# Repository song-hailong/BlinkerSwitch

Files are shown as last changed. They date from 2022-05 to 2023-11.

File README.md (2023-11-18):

# Blinker-Switch

通过改造墙壁开关，实现语音控制灯的效果。接入的平台为点灯科技，语音助手为小爱同学，可改造成天猫精灵和百度小度。

视频链接为： [【blinker】1：ESP8266点灯科技开发环境搭建](https://www.bilibili.com/video/BV1sk4y127Ab/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)  [【blinker】2：语音开关灯，墙壁开关改造篇！](https://www.bilibili.com/video/BV1dz4y1f7gt/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)

Blinker开发环境搭建可根据文档 **[点灯科技开发环境搭建](https://www.songhailong.cn/2022/05/%E7%82%B9%E7%81%AF%E7%A7%91%E6%8A%80%E5%BC%80%E5%8F%91%E7%8E%AF%E5%A2%83%E6%90%AD%E5%BB%BA/)** 进行操作。

PlatformIO IDE开发环境搭建可根据 [VSCode 下 PlatformIO 的安装教程](https://songhailong.cn/2023/01/VSCode%E4%B8%8BPlatformIO%E7%9A%84%E5%AE%89%E8%A3%85%E6%95%99%E7%A8%8B/) 进行安装。

---

# 常见问题：

1. 米家同步后无设备：需设备在线时点同步。
2. 米家APP设备页不显示该设备：点灯科技只能接入小爱同学，不能显示在米家主页，只会在其他平台设备页显示。如需设置与米家设备联动，可选择 **小爱音响 -> 自定义指令 -> 输入对应指令（如：”打开客厅的灯泡“） -> 选择静默执行**。

# 更新说明：

更新 3.0.2 版本代码，加入自动配网程序 [WiFiManager](https://github.com/song-hailong/WiFiManager) ，可以上传 key，不需修改代码，直接烧入后配网即可。

设置上电后连上WiFi `AutoConnectAP` ，在弹出的界面进行配网。

new ducument-300

## 一：项目文件介绍

#### 1. **Hardware**

Hardware文件夹为Blinker-Switch电路的原理图和PCB文件，提供Altium Designer格式的源文件。

#### 2. **Software**

Software文件夹为Blinker-Switch的程序源码。

2.1 **Arduino IDE**文件夹为初代程序代码，编译器为Arduino IDE，程序版本号为v2.0，推荐使用，对应的APP界面配置文件为：[界面配置_v2.0.txt](3.%20AppInterface/界面配置_v2.0.txt)。

2.2 **PlatformIO**为后续修改的代码，编译器使用的PlatformIO，程序版本号为v3.0，连续测试一个月后出现卡死，此版本上传数据太多，对于ESP8266来说容易卡死，目前不推荐使用，后续有时间进行优化。对应的APP界面配置文件为：[界面配置_v3.0.txt](3.%20AppInterface/界面配置_v3.0.txt)。

#### 3. AppInterface

AppInterface文件夹中提供了APP界面配置文件，版本号对应程序代码版本号。

#### 4. Docs

相关的参考文件，包括环境搭建和芯片的Datasheet等。

## 二：硬件说明

这款板子是零火版取电的，也就是86盒里面必须要有零线，如果没有的话，可以尝试加入单火取电模块，某宝有卖。

接线图如下：



> AC220V，一定一定要注意安全，一定要断电后操作。

## 三：程序说明

> 3.0.2 版本的代码已加入配网界面，可不修改代码，直接烧入。

将如下代码修改为自己的，设备密匙见下文。



**烧入**：选择对应的串口，以及开发板型号，将程序烧入即可。

## 四：APP配置

将界面配置文件导入到app设备中。

1. 在app中添加设备，获取Secret Key

   进入App，点击右上角的“+”号，然后选择添加设备，点击选择Arduino -> WiFi接入-> 选择要接入的服务商 -> 复制申请到的Secret Key

   Snipaste_2023-11-18_14-23-30

2. DIY界面

   在设备列表页，点击刚才新建的设备图标，进入设备控制面板。首次进入设备控制面板，会弹出向导页，在向导页点击载入示例，即可载入示例组件。点击右上角的修改，选择开关的按钮，样式选择中间那种，按键类型选择：开关按键，再点击有上角的保存。之后我们就可以通过这个按键来控制并查看灯。

   Snipaste_2023-11-18_14-31-04

3. 需导入我配置的界面的话，在APP中打开刚才新建的设备，点击右上角的 **... > 界面配置**，粘贴[界面配置_v2.0.txt](3.%20AppInterface/界面配置_v2.0.txt)中的配置代码即可。

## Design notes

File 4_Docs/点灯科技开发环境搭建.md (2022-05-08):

# 点灯科技开发环境配置
打包好的软件包阿里云链接：https://www.aliyundrive.com/s/KLycuo3tpkM （不定时更新，可到下方链接下载最新版本）。

## 一：安装 Arduino IDE

安装Arduino IDE 1.8.19或更新版本

软件安装包链接： https://www.arduino.cn/thread-5838-1-1.html （来自Arduino论坛）https://www.arduino.cc/en/software （来自官网）

由于某些原因，[Arduino官方网站](https://www.arduino.cc/en/Main/Software)经常打不开或下载速度极慢，推荐论坛下载，下载后安装即可。

## 二：安装ESP8266 SDK

Arduino IDE安装esp8266 SDK。在线安装经常出问题，推荐离线安装。下载链接：https://www.arduino.cn/thread-76029-1-1.html（来自Arduino论坛）。

该帖子里还有ESP32的SDK，可一并下载。下载之后需按照帖子里的要求进行操作：

1. 打开Arduino IDE菜单 > 文件 >首选项，在 **附加开发板管理器网址** 输入框中，填入以下网址：

``` 
https://www.arduino.cn/package_esp8266com_index.json,https://www.arduino.cn/package_esp32_index.jsonhttps://www.arduino.cn/package_esp32_index.json
```

> 若只需安装esp8266的SDK，则只需添加前一个网址即可。ESP32安装的论坛帖子链接为：https://www.arduino.cn/thread-81194-1-1.html。



2. 添加好后，再双击下载好的esp8266和esp32安装包，进行安装即可。

3. 安装好之后，重新打开Arduino IDE，打开 Arduino IDE **菜单 >工具>开发板**，就可以看到ESP8266和ESP32了。

   

## 三：下载blinker Arduino库

下载链接：https://github.com/blinker-iot/blinker-library/archive/refs/heads/dev_3.0.zip

将下载好的blinker库解压到：**我的电脑>文档>Arduino>libraries** 文件夹中



或者通过Arduino IDE进行导入：打开 Arduino IDE **菜单>项目>加载库>添加.ZIP库** ，如下图



两种方法选一种安装即可。

## 四：安装blinker APP

下载链接：https://diandeng.tech/dev



选择对应的安装包安装即可。

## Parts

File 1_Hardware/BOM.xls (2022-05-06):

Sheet: BOM Report
Bill of Materials |  |  | Bill of Materials for Project [ESP8266控制器.PrjPcb] (No PCB Document Selected)
Source Data From: |  | ESP8266控制器.PrjPcb
Project: |  | ESP8266控制器.PrjPcb
Variant: |  | None
Creation Date: | 2020/7/1 | 21:37
Print Date: | 2020-07-01 | 21:38:06
Footprint | Comment | LibRef | Designator | Description | Quantity
M3 125X200 | M3 | M3 | 1, 2, 3, 4 | 铜柱孔 | 4
C 0603_M | 100nF | C | C1 | 无极性贴片电容 | 1
C 0603_M | 104 | C | C2 | 无极性贴片电容 | 1
C 0603_M | 22p | C | C3, C4 | 无极性贴片电容 | 2
C 0603_M | 10uF | C | C5, C6 | 无极性贴片电容 | 2
SMA | SS14 | SS14 | D1, D2, D3 | 肖特基二极管 | 3
CD D(7343) | 100uF | C-CD | E1 | 贴片钽电容 | 1
CD D(7343) | 220uF | C-CD | E2 | 贴片钽电容 | 1
HK4100F | HK4100F-DC5V-SHG | HK4100F | JK1 | 一组转换 | 1
KF301-5.0-2P | HDR-1X2 | Header 2 5.0 | JP1, JP2 | 2P接插件 | 2
SOT23-3N | S8050 | 8050-SMD | Q1, Q2, Q3 | 高频放大-NPN型 | 3
R 0603_M | 12K | R | R1, R2, R3, R4, R5, R10, R11 | 贴片电阻 | 7
R 0603_M | 3k | R | R13, R14 | 贴片电阻 | 2
ESP_12_E_L | ESP_12_E | ESP_12_E | U1 | ESP-12 Wi-Fi Module by AI-Thinker | 1
SOP16_L | CH340G | CH340G | U2 | 串口转USB | 1
SOT223_L | AMS1117-3V3 | AMS1117 | U3 | 三端稳压芯片 | 1
HLK-PM01 | HLK-PM01 | Component_1 | U4 | 220V转5V模块 | 1
USB-MICRO_D | USB-5P | USB-5P | USB1 | 微型USB母座 | 1
OSC HC-49S | 12MHz | XTAL-2P | X1 | 2脚无源脚晶振 | 1
 |  |  |  |  | 36
Approved |  | Notes

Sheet: Project Information
Project Full Path | F:\Project\Altium Designer_Project\ESP8266联网控制器_v2\ESP8266控制器.PrjPcb
Project Filename | ESP8266控制器.PrjPcb
Variant Name | None
Data-Source Filename | ESP8266控制器.PrjPcb
Data-Source Full Path | F:\Project\Altium Designer_Project\ESP8266联网控制器_v2\ESP8266控制器.PrjPcb
Title | Bill of Materials for Project [ESP8266控制器.PrjPcb] (No PCB Document Selected)
Total Quantity | 36
Report Time | 21:37
Report Date | 2020/7/1
Report Date & Tine | 2020/7/1 21:37
Output Name | Bill of Materials
Output Type | BOM_PartType
Output Generator Name | BOM
Output Generator Description | Bill of Materials

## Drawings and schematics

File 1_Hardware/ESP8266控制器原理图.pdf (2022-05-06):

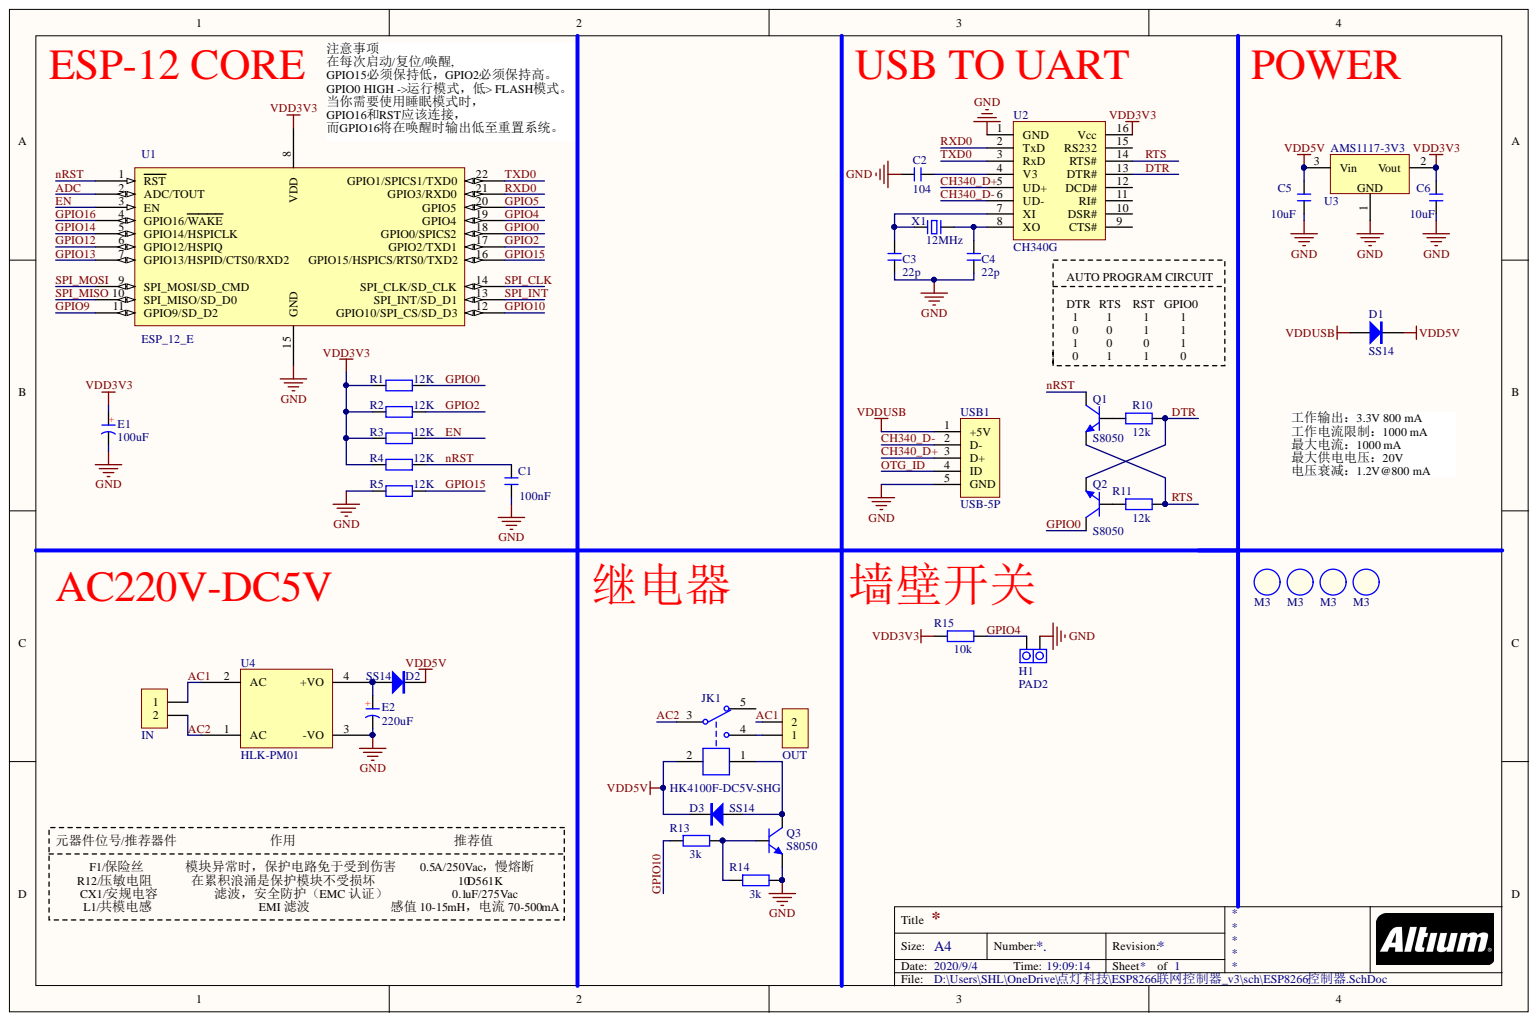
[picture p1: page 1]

Size: A4 | N umber: * . | Rev i s i o n : *
Date: 2 0 2 0 / 9 / 4 T ime: 1 9 : 0 9 : 1 4 | | Sheet * o f 1

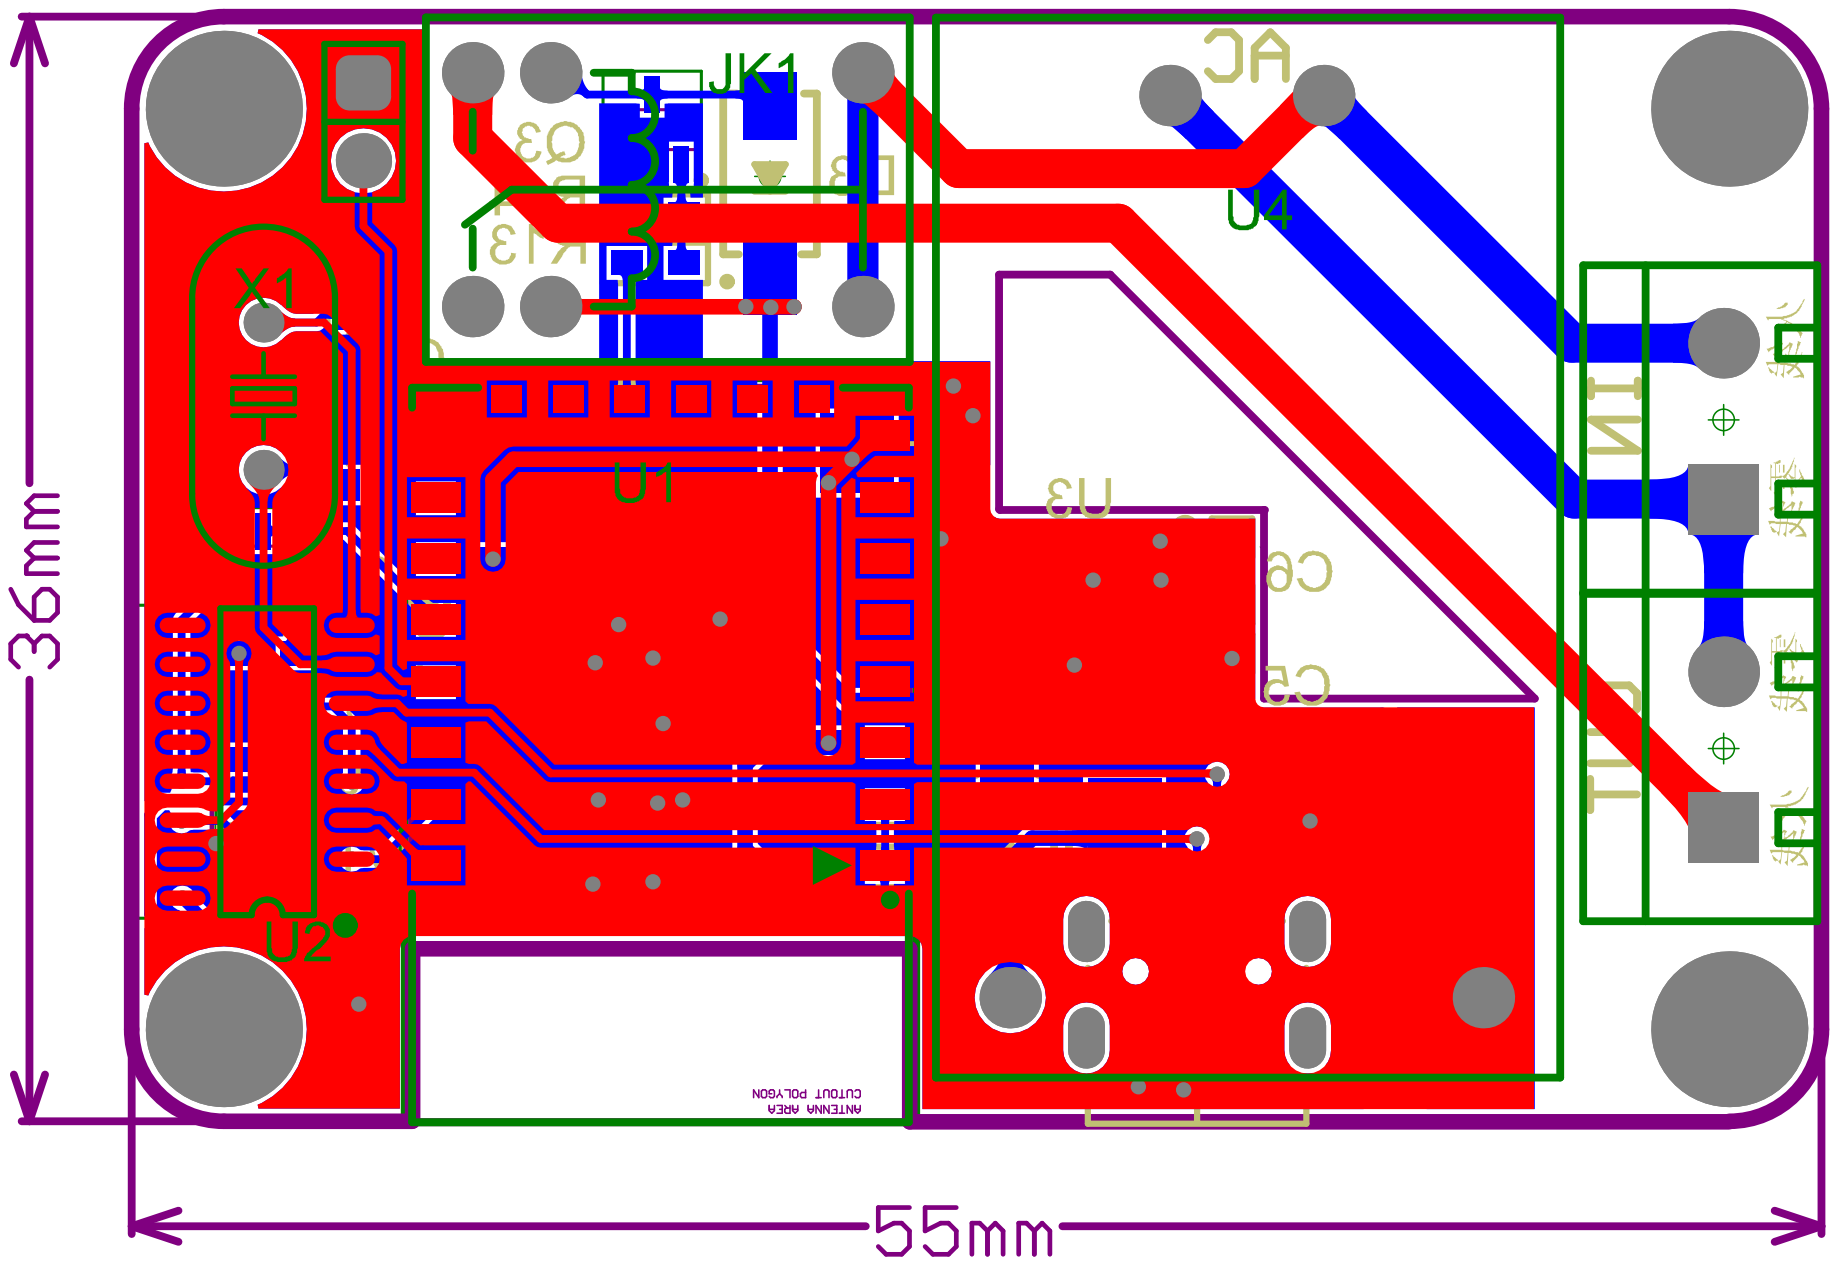
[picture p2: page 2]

Bill of Materials | Bill of Materialsfor Project[ESP8266控制器.PrjPcb](No PCBDocumentSelected)
Source Data From: | ESP8266控制器.PrjPcb
Project: | | ESP8266控制器.PrjPcb
Variant: | | None
Creation Date: 2020/9/4 | 19:09
Print Date: | 04-Sep-20 | 7:09:29 PM
Footprint | Comment | LibRef | Designator | Description | Quantity
M3 125X200 M3 | M3 | 1, 2, 3, 4 | 铜柱孔 | 4
C 0603_M | 100nF | C | C1 | 无极性贴片电容 | 1
C 0603_M | 104 | C | C2 | 无极性贴片电容 | 1
C 0603_M | 22p | C | C3, C4 | 无极性贴片电容 | 2
C 0603_M | 10uF | C | C5, C6 | 无极性贴片电容 | 2
SMA | SS14 | SS14 | D1, D2, D3 | 肖特基二极管 | 3
CD D(7343) 100uF | C-CD | E1 | 贴片钽电容 | 1
CD D(7343) 220uF | C-CD | E2 | 贴片钽电容 | 1
PAD2-2.54 | PAD2 | PAD2 | H1 | 引线焊盘 | 1
KF301-5.0-2PHDR-1X2 | Header 2 5.0 | IN, OUT | 2P接插件 | 2
HK4100F | HK4100F-DC5V-HK4100F | JK1 | 一组转换 | 1
SOT23-3N | S8050 | 8050-SMD | Q1, Q2, Q3 | 高频放大-NPN型 | 3
R 0603_M | 12K | R | R1, R2, R3, R4, R5, R10, R11 | 贴片电阻 | 7
R 0603_M | 3k | R | R13, R14 | 贴片电阻 | 2
R 0603_M | 10k | R | R15 | 贴片电阻 | 1
ESP_12_E_L ESP_12_E | ESP_12_E | U1 | ESP-12 Wi-Fi Module by AI-Thinker | 1
SOP16_L | CH340G | CH340G | U2 | 串口转USB | 1
SOT223_L | AMS1117-3V3 | AMS1117 | U3 | 三端稳压芯片 | 1
HLK-PM01 | HLK-PM01 | Component_1 | U4 | 220V转5V模块 | 1
USB-MICRO_DUSB-5P | USB-5P | USB1 | 微型USB母座 | 1
OSC HC-49S 12MHz | XTAL-2P | X1 | 2脚无源脚晶振 | 1
| | | | | 38
Approved | | Notes

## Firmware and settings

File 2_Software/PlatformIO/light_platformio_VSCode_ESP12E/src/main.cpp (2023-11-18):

#define BLINKER_WIFI
#define BLINKER_MIOT_LIGHT//支持小爱同学
#define BLINKER_OTA_VERSION_CODE "3.0.2" //版本号
#include <Arduino.h>
#include <Blinker.h>
#include <WiFiManager.h> // https://github.com/tzapu/WiFiManager
#include "main.h"

char auth[BLINKER_AUTHKEY_SIZE] = ""; // app中获取到的Secret Key(密钥)
char ssid[BLINKER_SSID_SIZE] = "";  // WIFI名称
char pswd[BLINKER_PSWD_SIZE] = "";    // WIFI密码

MyLightState LightState; //灯的状态
WiFiManager wm; //初始化WiFiManager

// 新建组件对象
#define BUTTON_Light (char*)"btn-light"
BlinkerButton ButtonLight(BUTTON_Light);                 // 按键组件：开/关灯
BlinkerText TextLightState((char*)"tex-state");          // 文字组件：显示灯的状态
BlinkerText TextBlinkerTime((char*)"tex-BlinkerTime");   // 文字组件：显示系统运行时间
BlinkerNumber NumberSignal((char*)"num-signal");         // 数据组件：显示WiFi信号强度
BlinkerText TextStateChange((char*)"tex-change");        // 文字组件：显示灯状态改变原因
BlinkerText TextStateChange1((char*)"tex-change1");      // 文字组件：显示灯状态改变原因1
BlinkerText TextStateChange2((char*)"tex-change2");      // 文字组件：显示灯状态改变原因2
BlinkerText TextStateChange3((char*)"tex-change3");      // 文字组件：显示灯状态改变原因3
BlinkerText TextStateChange4((char*)"tex-change4");      // 文字组件：显示灯状态改变原因4

// 首页开关的回调函数, 当收到指令时会调用该回调函数
void switch_callback(const String & state)
{
  BLINKER_LOG("get switch state: ", state);

  if (state == BLINKER_CMD_ON)
  {
    LightState.OpenCloseLight(ONLight, APPSwitchON); // 开灯
  }
  else
  {
    LightState.OpenCloseLight(OFFLight, APPSwitchOFF); // 关灯
  }
}

// 开关灯按键回调函数，当收到指令时会调用该回调函数
void BUTTONLight_callback(const String & state)
{
  BLINKER_LOG("get button state: ", state);

  if (state == BLINKER_CMD_ON)
  {
    LightState.OpenCloseLight(ONLight, APPButtonON); // 开灯
  }
  else
  {
    LightState.OpenCloseLight(OFFLight, APPButtonOFF); // 关灯
  }
  Blinker.vibrate();//发送手机振动指令
}

//小爱电源类操作的回调函数:
//当小爱同学向设备发起控制, 设备端需要有对应控制处理函数
void miotPowerState(const String & state)
{
  BLINKER_LOG("need set power state: ", state);
  if (state == BLINKER_CMD_ON)
  {
    BlinkerMIOT.powerState("on"); //给小爱同学反馈控制状态：已打开
    BlinkerMIOT.print();

    LightState.OpenCloseLight(ONLight, XIAOMIAION); // 开灯
  }
  else if (state == BLINKER_CMD_OFF)
  {
    BlinkerMIOT.powerState("off"); //给小爱同学反馈控制状态：已关闭
    BlinkerMIOT.print();

    LightState.OpenCloseLight(OFFLight, XIAOMIAIOFF); // 关灯
  }
}
// 用户自定义设备查询的回调函数:
void miotQuery(int32_t queryCode)
{
    BLINKER_LOG("MIOT Query codes: ", queryCode);

    switch (queryCode)
    {
        case BLINKER_CMD_QUERY_ALL_NUMBER :
            BLINKER_LOG("MIOT Query All");
            BlinkerMIOT.powerState(LightState.LedState ? "on" : "off");
            BlinkerMIOT.print();
            break;
        case BLINKER_CMD_QUERY_POWERSTATE_NUMBER :
            BLINKER_LOG("MIOT Query Power State");
            BlinkerMIOT.powerState(LightState.LedState ? "on" : "off");
            BlinkerMIOT.print();
            break;
        default :
            BlinkerMIOT.powerState(LightState.LedState ? "on" : "off");
            BlinkerMIOT.print();
            break;
    }
}

// 如果未绑定的组件被触发，则会执行其中内容
void dataRead(const String & data)
{
  BLINKER_LOG("Blinker readString: ", data);
  Blinker.vibrate();  //发送手机振动指令
}

// 用户自定义状态返回的心跳包回调函数
void heartbeat()
{
  BUILTIN_SWITCH.print(LightState.LedState ? "on" : "off"); //开/关组件
  //灯泡  <i class="far fa-lightbulb"></i>
  //灯泡亮<i class="far fa-lightbulb-on"></i>
  ButtonLight.icon(LightState.LedState ? "far fa-lightbulb-on" : "far fa-lightbulb"); //设置图标
  ButtonLight.color(LightState.LedState ? "Blue" : "Black");  //设置颜色
  ButtonLight.print(LightState.LedState ? "on" : "off"); // 按键组件
  //天花灯 <i class="fad fa-light-ceiling"></i>
  TextLightState.icon("fad fa-light-ceiling");
  TextLightState.color(LightState.LedState ? "Blue" : "Black");
  TextLightState.print(LightState.LedState ? " 开启 " : " 关闭 ");

  char SprintfChar[25];
  sprintf(SprintfChar, "%lld天%lld时%lld分", 
          LightState.RunTime/3600/24,LightState.RunTime/3600%24,LightState.RunTime/60%60);
  //卡车时钟图标 <i class="far fa-shipping-timed"></i>
  TextBlinkerTime.icon("far fa-shipping-timed");       
  TextBlinkerTime.print(SprintfChar/*,"系统运行时间"*/);

  //无信号  <i class="fad fa-wifi-slash"></i>
  //1格信号 <i class="fad fa-wifi-1"></i>
  //2格信号 <i class="fad fa-wifi-2"></i>
  //3格信号 <i class="fad fa-wifi"></i>
  NumberSignal.icon("fad fa-wifi");
  //NumberSignal.color("Green");  //LimeGreen
  //NumberSignal.unit("Dbm");
  NumberSignal.print(LightState.SignalStrength);//信号强度

  //问号 <i class="far fa-question"></i>
  //TextStateChange.icon("far fa-question");
  //TextStateChange.color("MediumPurple");
  //TextStateChange.print("灯泡状态改变的原因");
  
  //重复箭头 <i class="fad fa-repeat-alt"></i>
  //语音 <i class="fad fa-microphone"></i>
  //手机 <i class="far fa-mobile-android"></i>
  //开关 <i class="far fa-light-switch"></i>
  if(LightState.LightStateChange[0] == APPSwitchON || LightState.LightStateChange[0] == APPSwitchOFF || 
     LightState.LightStateChange[0] == APPButtonON || LightState.LightStateChange[0] == APPButtonOFF)
    TextStateChange1.icon("far fa-mobile-android");//手机
  else if(LightState.LightStateChange[0] == XIAOMIAION || LightState.LightStateChange[0] == XIAOMIAIOFF)
    TextStateChange1.icon("fad fa-microphone");//语音
  else if (LightState.LightStateChange[0] == WallSwitchON || LightState.LightStateChange[0] == WallSwitchOFF)
    TextStateChange1.icon("far fa-light-switch");//开关
  else
    TextStateChange1.icon("fad fa-repeat-alt");//重复箭头
  //TextStateChange1.color("Purple");
  TextStateChange1.print(LightState.LightStateChangeWord[0]);


  if(LightState.LightStateChange[1] == APPSwitchON || LightState.LightStateChange[1] == APPSwitchOFF || 
     LightState.LightStateChange[1] == APPButtonON || LightState.LightStateChange[1] == APPButtonOFF)
    TextStateChange2.icon("far fa-mobile-android");//手机
  else if(LightState.LightStateChange[1] == XIAOMIAION || LightState.LightStateChange[1] == XIAOMIAIOFF)
    TextStateChange2.icon("fad fa-microphone");//语音
  else if (LightState.LightStateChange[1] == WallSwitchON || LightState.LightStateChange[1] == WallSwitchOFF)
    TextStateChange2.icon("far fa-light-switch");//开关
  else
    TextStateChange2.icon("fad fa-repeat-alt");//重复箭头
  //TextStateChange2.color("Purple");
  TextStateChange2.print(LightState.LightStateChangeWord[1]);


  if(LightState.LightStateChange[2] == APPSwitchON || LightState.LightStateChange[2] == APPSwitchOFF || 
     LightState.LightStateChange[2] == APPButtonON || LightState.LightStateChange[2] == APPButtonOFF)
    TextStateChange3.icon("far fa-mobile-android");//手机
  else if(LightState.LightStateChange[2] == XIAOMIAION || LightState.LightStateChange[2] == XIAOMIAIOFF)
    TextStateChange3.icon("fad fa-microphone");//语音
  else if (LightState.LightStateChange[2] == WallSwitchON || LightState.LightStateChange[2] == WallSwitchOFF)
    TextStateChange3.icon("far fa-light-switch");//开关
  else
    TextStateChange3.icon("fad fa-repeat-alt");//重复箭头
  //TextStateChange3.color("Purple");
  TextStateChange3.print(LightState.LightStateChangeWord[2]);


  if(LightState.LightStateChange[3] == APPSwitchON || LightState.LightStateChange[3] == APPSwitchOFF || 
     LightState.LightStateChange[3] == APPButtonON || LightState.LightStateChange[3] == APPButtonOFF)
    TextStateChange4.icon("far fa-mobile-android");//手机
  else if(LightState.LightStateChange[3] == XIAOMIAION || LightState.LightStateChange[3] == XIAOMIAIOFF)
    TextStateChange4.icon("fad fa-microphone");//语音
  else if (LightState.LightStateChange[3] == WallSwitchON || LightState.LightStateChange[3] == WallSwitchOFF)
    TextStateChange4.icon("far fa-light-switch");//开关
  else
    TextStateChange4.icon("fad fa-repeat-alt");//重复箭头
  //TextStateChange4.color("Purple");
  TextStateChange4.print(LightState.LightStateChangeWord[3]);

  BLINKER_LOG("heartbeat!");
}


void setup()
{
    // 初始化串口，并开启调试信息，调试用可以删除
    Serial.begin(115200);
    BLINKER_DEBUG.stream(Serial);

    // 初始化IO
    pinMode(relay, OUTPUT);
    digitalWrite(relay, LOW);
    pinMode(KEY, INPUT);
    digitalWrite(KEY, HIGH);
    LightState.WallSwitchState = digitalRead(KEY);  // 获取墙壁开关此时的状态

    delay(2000);
    BLINKER_LOG("ok!");

    EEPROM.begin(BLINKER_EEP_SIZE);
    EEPROM.get(2448, auth);
    EEPROM.commit();
    EEPROM.end();
    Serial.println(auth);

//    wm.resetSettings(); // 清除保存的WiFi信息，这些信息为esp library进行储存

    if (strlen(ssid) == 0) {
        //    尝试使用已保存的WiFi连接凭据自动连接WiFi；
        //    如果连接失败，将自动创建一个具有指定名称的访问点（如果名称为空，则会自动生成SSID），如果密码为空，则为匿名访问点；
        //    进入阻塞循环等待配置，并返回成功结果。
        bool res;
        res = wm.autoConnect("AutoConnectAP"); // anonymous ap
        if (!res) { //AP配网失败
            Serial.println("Failed to connect");
            ESP.restart(); // 重启复位esp32
        } else { //AP配网成功
            Serial.println("connected...yeey :)");
            if (wm._auth != "") {
                memcpy(auth,wm._auth.c_str(),BLINKER_AUTHKEY_SIZE);
                EEPROM.begin(BLINKER_EEP_SIZE);
                EEPROM.put(2448, auth);
                EEPROM.commit();
                EEPROM.end();
            }
            memcpy(ssid,wm.getWiFiSSID().c_str(),BLINKER_SSID_SIZE);
            memcpy(pswd,wm.getWiFiPass().c_str(),BLINKER_PSWD_SIZE);
        }
    }

    // 初始化blinker
    Blinker.begin(auth, ssid, pswd);
    Blinker.attachData(dataRead); //注册回调函数，当有设备收到APP发来的数据时会调用对应的回调函数
    Blinker.attachHeartbeat(heartbeat);//注册心跳包回调函数
    BUILTIN_SWITCH.attach(switch_callback); //设置首页开关的回调函数, 当收到指令时会调用该回调函数
    ButtonLight.attach(BUTTONLight_callback);//注册开关灯按键的回调函数, 当收到指令时会调用该回调函数

    //给APP发送当前的状态
    heartbeat();

    //小爱同学务必在回调函数中反馈该控制状态
    BlinkerMIOT.attachPowerState(miotPowerState);//注册小爱电源类的操作接口回调函数
    BlinkerMIOT.attachQuery(miotQuery);  //注册小爱设备查询接口回调函数
}

void loop()
{
    Blinker.run();

    //墙壁开关的控制
    LightState.WallSwitchControl();

    if(millis() - LightState.LastGetDataTime >= 500) //距上次获取数据已经过去0.5s
    {
        LightState.LastGetDataTime = millis();   // 更新获取数据时间，单位为毫秒（ms）
        LightState.RunTime = LightState.LastGetDataTime/1000;  // 获取设备运行时间, 单位为秒(s)
        LightState.SignalStrength = WiFi.RSSI(); // WIFI信号强度
    }

    if (LightState.SwitchNum >= LightState.SwitchNumReset){
        wm.resetSettings(); // 清除保存的WiFi信息，这些信息为esp library进行储存
        ESP.restart(); // 重启复位esp32
    }
}


//获取当前时间
bool mytime::GetNowTime()
{
  int8_t  sec = Blinker.second();  //秒
  int8_t  min = Blinker.minute();  //分
  int8_t  hour = Blinker.hour();   //时
  int8_t  wday = Blinker.wday();   //周几 0-6(依次为周日/一/二/三/四/五/六)
  int8_t  mday = Blinker.mday();   //当月第几天  1-31
  int16_t yday = Blinker.yday();   //当年第几天  1-366
  int8_t  month = Blinker.month(); //月份
  int16_t year = Blinker.year();   //年份

  if( sec != -1 && min != -1 && hour != -1 && wday != -1 && mday != -1 && yday != -1 && month != -1 && year != -1)
  {
    this->My_sec = sec;
    this->My_min = min;
    this->My_hour = hour;
    this->My_wday = wday;
    this->My_mday = mday;
    this->My_yday = yday;
    this->My_month = month;
    this->My_year = year;

    this->is_ok = true;
  }
  else
    this->is_ok = false;

  return this->is_ok;
}

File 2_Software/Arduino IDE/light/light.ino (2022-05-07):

/*xxxx的灯泡*/
#define BLINKER_WIFI
#define BLINKER_MIOT_LIGHT//支持小爱同学
#define BLINKER_OTA_VERSION_CODE "2.0.0"
#include <Blinker.h>

char auth[] = "xxxxxxxx";//app中获取到的Secret Key(密钥)
char ssid[] = "xxxxxxxx";//WIFI账号
char pswd[] = "xxxxxxxx";//WIFI密码

// 设置各引脚别名
#define GPIO 10 // 定义继电器输入引脚为GPIO/10
#define KEY 4 // 定义按键引脚
// 变量定义
bool State = 0; // 存储墙壁开关状态的变量
bool led_state = false;// 存储灯状态的变量

// 新建组件对象
BlinkerButton Button1("btn-abc");//注意：要和APP组件’数据键名’一致
BlinkerText Text1("tex-30b");


void switch_callback(const String & state)
{
  BLINKER_LOG("get switch state: ", state);

  if (state == BLINKER_CMD_ON)
  {
    led_state = true;
    digitalWrite(GPIO, HIGH);
    BUILTIN_SWITCH.print("on"); //发送开关当前的状态(多用于反馈开关状态)到APP
    Button1.print("on");
    Text1.color(led_state ? "Blue" : "black");
    Text1.print(led_state ? "灯状态: 开启" : "灯状态: 关闭");
  }
  else
  {
    led_state = false;
    digitalWrite(GPIO, LOW);
    BUILTIN_SWITCH.print("off");
    Button1.print("off");
    Text1.color(led_state ? "Blue" : "black");
    Text1.print(led_state ? "灯状态: 开启" : "灯状态: 关闭");
  }
}

// 按下BlinkerAPP按键即会执行该函数
void button1_callback(const String & state)
{
  BLINKER_LOG("get button state: ", state);

  if (state == BLINKER_CMD_ON)
  {
    led_state = true;
    digitalWrite(GPIO, HIGH);
    BUILTIN_SWITCH.print("on"); //发送开关当前的状态(多用于反馈开关状态)到APP
    Button1.print("on");

    Text1.color(led_state ? "Blue" : "black");
    Text1.print(led_state ? "灯状态: 开启" : "灯状态: 关闭");
  }
  else
  {
    led_state = false;
    digitalWrite(GPIO, LOW);
    BUILTIN_SWITCH.print("off");
    Button1.print("off");

    Text1.color(led_state ? "Blue" : "black");
    Text1.print(led_state ? "灯状态: 开启" : "灯状态: 关闭");
  }
  Blinker.vibrate();//发送手机振动指令
}



//小爱电源类操作的回调函数:
//当小爱同学向设备发起控制, 设备端需要有对应控制处理函数
void miotPowerState(const String & state)
{
  BLINKER_LOG("need set power state: ", state);
  if (state == BLINKER_CMD_ON)
  {
    digitalWrite(GPIO, HIGH);
    BlinkerMIOT.powerState("on");
    BlinkerMIOT.print();

    led_state = true;
    Button1.print("on");
    BUILTIN_SWITCH.print("on");
    Text1.color(led_state ? "Blue" : "black");
    Text1.print(led_state ? "灯状态: 开启" : "灯状态: 关闭");
  }
  else if (state == BLINKER_CMD_OFF)
  {
    digitalWrite(GPIO, LOW);
    BlinkerMIOT.powerState("off");
    BlinkerMIOT.print();

    led_state = false;
    Button1.print("off");
    BUILTIN_SWITCH.print("off");
    Text1.color(led_state ? "Blue" : "black");
    Text1.print(led_state ? "灯状态: 开启" : "灯状态: 关闭");
  }
}

//当有设备收到APP发来的数据时会调用该函数
void dataRead(const String & data)
{
  BLINKER_LOG("Blinker readString: ", data);

  Blinker.vibrate();

  uint32_t BlinkerTime = millis();

  Blinker.print("millis", BlinkerTime);
}


/*
   在此函数中添加您的心跳消息详细信息

   当get heartbeat命令{“get”:“state”}时，设备将调用此函数
   例如，您可以打印回消息

   Every 30s will get a heartbeat command from app
*/
void heartbeat()
{
  BUILTIN_SWITCH.print(led_state ? "on" : "off");
  Button1.print(led_state ? "on" : "off");
  Text1.color(led_state ? "Blue" : "black");
  Text1.print(led_state ? "灯状态: 开启" : "灯状态: 关闭");

  BLINKER_LOG("heartbeat!");
}


void setup()
{
  // 初始化串口，并开启调试信息，调试用可以删除
  Serial.begin(115200);
  BLINKER_DEBUG.stream(Serial);
  // 初始化IO
  pinMode(GPIO, OUTPUT);
  digitalWrite(GPIO, LOW);
  pinMode(KEY, INPUT);
  digitalWrite(KEY, HIGH);

  State = digitalRead(KEY);
  led_state = false;


  // 初始化blinker
  Blinker.begin(auth, ssid, pswd);
  Blinker.attachData(dataRead); //注册回调函数，当有设备收到APP发来的数据时会调用对应的回调函数
  Blinker.attachHeartbeat(heartbeat);//注册心跳包回调函数
  BUILTIN_SWITCH.attach(switch_callback); //设置开关的回调函数, 当收到指令时会调用该回调函数
  Button1.attach(button1_callback);//注册按键的回调函数, 当收到指令时会调用该回调函数

  //给APP发送当前的状态
  BUILTIN_SWITCH.print(led_state ? "on" : "off");
  Button1.print(led_state ? "on" : "off");
  Text1.color(led_state ? "Blue" : "black");
  Text1.print(led_state ? "灯状态: 开启" : "灯状态: 关闭");

  //小爱同学务必在回调函数中反馈该控制状态
  BlinkerMIOT.attachPowerState(miotPowerState);//注册回调函数
}

void loop()
{
  Blinker.run();

  //墙壁开关的控制指令
  if (digitalRead(KEY) != State)
  {
    delay(100);
    if (digitalRead(KEY) != State)
    {
      State = digitalRead(KEY);
      digitalWrite(GPIO, !digitalRead(GPIO));
      led_state = !led_state;//改变存储灯状态的变量

      BUILTIN_SWITCH.print(led_state ? "on" : "off");
      Button1.print(led_state ? "on" : "off");
      Text1.color(led_state ? "Blue" : "black");
      Text1.print(led_state ? "灯状态: 开启" : "灯状态: 关闭");

      delay(200);
    }
  }
}

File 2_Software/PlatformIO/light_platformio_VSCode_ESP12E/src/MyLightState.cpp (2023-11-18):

#include "MyLightState.h"

//当前时间 
mytime NowTime;  

struct MenuChange Menu[] = {
    {0 , "APPSwitchON"  , "通过APP首页按键打开",},
    {1 , "APPSwitchOFF" , "通过APP首页按键关闭"},
    {2 , "APPButtonON"  , "通过APP开关按键打开",},
    {3 , "APPButtonOFF" , "通过APP开关按键关闭",},
    {4 , "XIAOMIAION"   , "通过小爱同学打开",},
    {5 , "XIAOMIAIOFF"  , "通过小爱同学关闭",},
    {6 , "WallSwitchOFF" , "通过墙壁开关关闭",},
    {7 , "WallSwitchON", "通过墙壁开关打开",},
};

MyLightState::MyLightState()
{
//    this->WallSwitchState = digitalRead(KEY);  // 获取墙壁开关此时的状态
    this->LedState = false;     // 灯默认为关闭
    this->SignalStrength = 0.0; // 信号强度
    this->RunTime = 0;   // 系统运行时间 单位s
    this->LastGetDataTime = 0; // 上次获取数据时间 单位ms
    //储存灯状态发生改变的原因，指定大小为4
    this->LightStateChange.resize(4, -1);
    //储存用于显示 灯状态发生改变原因的 文字，只存4次
    this->LightStateChangeWord.resize(4, "**********");

    SwitchNum = 0; // SwitchNumResetInTime秒钟内开关按下的次数
    Switch1NumTime = 0; // 首次按下时间
    SwitchNumReset = 5; // 按 SwitchNumReset 次重置
    SwitchNumResetInTime = 2; // 在 SwitchNumResetInTime 秒内按 SwitchNumReset 次重置
}

// 开/关灯函数
// 参数：
//       ON_OFF   ：  开 ||  关灯
//       ChangeReason  ：改变的原因
void MyLightState::OpenCloseLight(bool ON_OFF, uint8_t ChangeReason)
{
    if(ON_OFF != this->LedState) // 如果灯当前的状态与需要切换的状态不一致
    {
        digitalWrite(relay, ON_OFF);  // 开/关灯
        this->LedState = ON_OFF;      // 切换灯的状态

        NowTime.GetNowTime();

        String ChangeArray;
        char SprintfChar[30];
        sprintf(SprintfChar,"%d年%0d月%0d日 %02d:%02d:%02d ",
                NowTime.My_year, NowTime.My_month, NowTime.My_mday, 
                NowTime.My_hour, NowTime.My_min, NowTime.My_sec);
        ChangeArray = SprintfChar;
        ChangeArray += Menu[ChangeReason].name;
        // 储存灯状态发生改变的原因
        //尾删
        this->LightStateChange.pop_back();
        this->LightStateChangeWord.pop_back();
        //在头部插入当前状态发生改变的原因
        this->LightStateChange.insert(LightStateChange.begin(), ChangeReason);
        this->LightStateChangeWord.insert(LightStateChangeWord.begin(), ChangeArray);
        heartbeat();                // 更新app显示
    }
}


// 墙壁开关的控制函数
void MyLightState::WallSwitchControl()
{
    if (digitalRead(KEY) != this->WallSwitchState) //如果墙壁开关当前状态发生改变
    {
        delay(100); //延时消抖
        if (digitalRead(KEY) != this->WallSwitchState)
        {
            this->WallSwitchState = digitalRead(KEY); //记录墙壁开关当前的状态

            if (SwitchNum == 0) //如果是第一次按下，记录当前时间
                Switch1NumTime = millis();
            SwitchNum++;
//            Serial.print("SwitchNum = ");
//            Serial.println(SwitchNum);

            this->OpenCloseLight(!(this->LedState), (!(this->LedState)) + 6);
        }
    }
    if (SwitchNum !=0 && millis() - Switch1NumTime > SwitchNumResetInTime*1000) // SwitchNumResetInTime秒钟后按键按下次数清零
        SwitchNum = 0;
}

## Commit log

2021-09-02 Create 软件包
2021-09-02 V2.0
    1. 添加PCB工程文件和原理图文件
    2. 提供软件包下载链接
    [BOM.xls, ESP8266控制器.PrjPcb, ESP8266控制器.SchDoc]
2022-03-08 添加界面
2022-03-08 添加界面文件，界面版本对应程序版本
2022-05-06 更新 readme
    [BOM.xls, ESP8266控制器.PrjPcb, ESP8266控制器.SchDoc]
2022-05-06 修改readme
    [BOM.xls, ESP8266控制器.PrjPcb, ESP8266控制器.SchDoc]
2022-05-07 修复 墙壁开关连接的引脚为 IO4
    [ESP8266控制器.PrjPcb, ESP8266控制器.SchDoc, esp8266_pin_list.xls]
2022-05-13 修改PCB
    1. 增加logo
    2. 修改墙壁开关接线接口
    3. 修改原理图布局
    [ESP8266控制器.SchDoc]
2022-05-13 Update README.md
    增加 常见问题 部分
2022-05-22 Update README.md
    添加问题2
2022-07-25 移动 .gitattributes 文件
2023-01-14 修改ReadMe，增加PlatformIO安装教程
    [BOM.xls, ESP8266控制器.PrjPcb, ESP8266控制器.SchDoc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]
2023-01-24 修改PlatformIO版本程序及界面
2023-11-18 更新软件3.0.2版本
    1. 增加自动配网代码。
    2. 修改ReadMe。
    3. 更改路径文件。
    [BOM.xls, ESP8266控制器.PrjPcb, ESP8266控制器.SchDoc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]
